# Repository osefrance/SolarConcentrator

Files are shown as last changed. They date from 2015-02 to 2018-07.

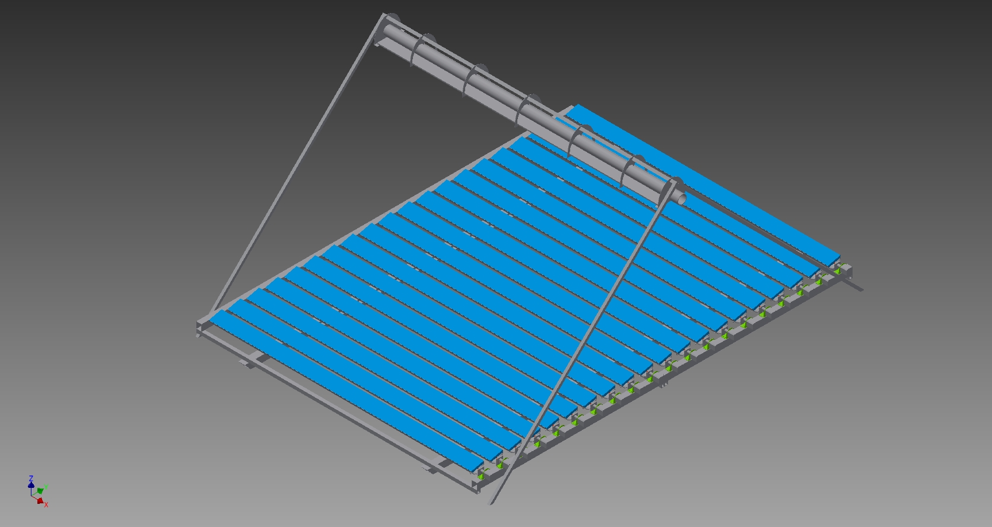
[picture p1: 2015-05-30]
Design3D/Inventor/Assemblage_général_N-S.jpg

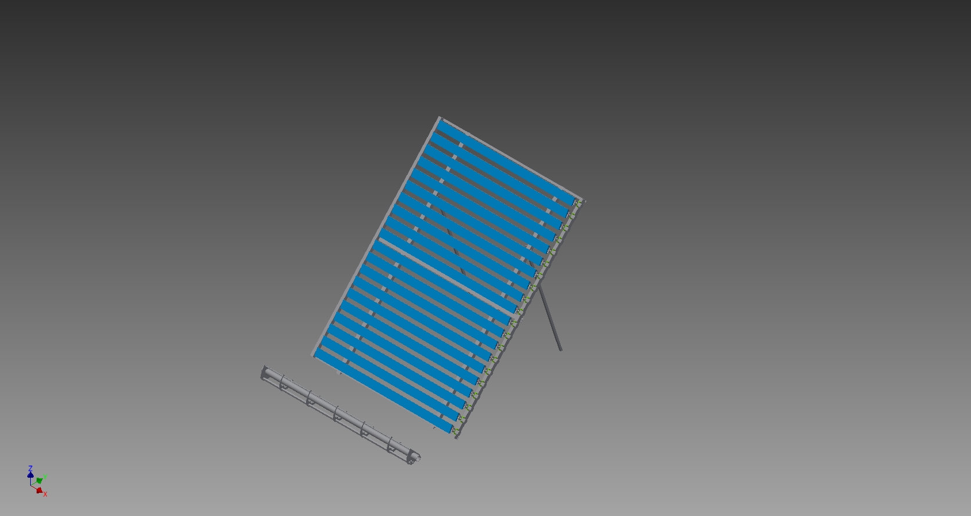
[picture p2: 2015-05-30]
Design3D/Inventor/Assemblage_général_E-O.jpg

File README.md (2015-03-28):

# SolarConcentrator
Open Hardware Solar concentrator - Linear Fresnel Reflector

The OSÉ Solar concentrator programs and designs are licensed under the GPL V2, GPL V3 or 
Attribution-ShareAlike 4.0 International based on the most appropriate license for the type of work.

The full text of the license GPL is available here:  
http://www.gnu.org/licenses/old-licenses/gpl-2.0.html
http://choosealicense.com/licenses/gpl-3.0/
The creative common license is available here http://creativecommons.org/licenses/by-sa/4.0/

See also:
     http://en.wikipedia.org/wiki/GPL 

more information on this open hardware Solar concentrator can be found here: http://wiki.osefrance.org/doku.php?id=wiki:concentrateursolaire

its authors are voulunteers of Open Source Ecologie (French chapter of Open Source Ecology) www.osefrance.fr

#Présentation générale
#Objectif

L'objectif du projet est de fabriquer un concentrateur solaire, c'est à dire, un dispositif permettant de collecter l'énergie thermique solaire, c'est à dire :

    capter et concentrer le flux solaire sur un absorbeur,
    assurer l'extraction de la chaleur pour son utilisation a posteriori.

Les usages et grandeurs de référence sont définies par la suite.
Contexte

Le développement du produit aura lieu au sein de l'association Open Source Écologie en collaboration avec toute personne se sentant un lien pour le projet. Il sera réalisé de manière à s'inscrire dans le contexte de l'économie open source sans contrevenir aux dispositions de la propriété intellectuelle (brevets existants) et aux normes en vigueur (dispositif sous pression).

Le concentrateur solaire a été sélectionné parmi les 50 machines du Global Village Construction Set (GVCS). Il fait partie des dispositifs permettant la production primaire d'énergie.

Le changement climatique et la dépendance actuelle aux énergies fossiles nous montrent la nécessité d'une transition écologique où les énergies renouvelables, et en particulier le solaire thermique, doivent jouer un rôle prépondérant. De plus, le choix du solaire thermique est motivé par le constat que environ 40% de l'énergie consommée par l'industrie en Europe est utilisée pour générer de la chaleur à des températures inférieures à 400°C.
Utilisation : usages et finalité

Nous préparons un développement en plusieurs étapes pour apprendre et progresser au fur et à mesure. Pendant les phases de design 3D et de développement, nous prévoyons de construire une maquette de table pour tester la forme générale et l’automatisation. Ensuite, un démonstrateur sera présenté pendant le forum Alternatiba, le 26 septembre 2015. Enfin, au cours de l’année 2016, un prototype grandeur nature (de 10 à 15 m²) sera conçu sur la base des connaissances engrangées.
#Démonstrateur (phase actuelle)

L'objectif est de présenter la technique de la concentration solaire dans un but de diffusion des savoirs et de sensibilisation. Il est nécessaire d'aboutir à un produit fonctionnel, d'encombrement réduit, fonctionnant en France. La température atteinte sera fonction des optiques concentration et de la surface de miroir mais n'est pas une exigence.
Prototype

Les prototypes seront conçus pour une finalité productive, adaptables sur une large plage de latitudes et dans des lieux isolés. Les usages visés sont variés : cuisson, procédés artisanaux ou industriels utilisant de la chaleur moyenne température (250°C max).
Solution retenue

Il existe différentes technologies de concentration du rayonnement solaire.

Schéma du concentrateur et définition des axes. (1) Miroir de Fresnel ou collecteur; (2) facettes du miroir; (3) récepteur.

La solution que nous avons retenue est un concentrateur solaire plan, à symétrie axiale, avec deux étages de concentration. La concentration primaire est réalisée par un miroir de Fresnel, la concentration secondaire par un concentrateur parabolique composé (CPC) sur l'absorbeur situé au foyer. Cette solution a été retenue pour sa simplicité de fabrication et d'utilisation.

Plus précisément, le miroir de Fresnel ou collecteur (1) concentre le rayonnement sur une ligne sur laquelle se trouve le récepteur (3). L'orientation globale du concentrateur solaire (CS) est fixée par l'axe du récepteur (axe x). Le suivi solaire selon un axe perpendiculaire (axe y) peut être réalisé aisément grâce à la rotation des facettes (3) du miroir de Fresnel. Par contre, la variation d'angle d'incidence parallèle à l'axe du CS (saisonnier ET quotidien) induit une translation entre l'image réfléchie par le collecteur et le récepteur, c'est à dire des pertes supplémentaires aux extrémités du récepteur (end loss).

Figure: schéma du concentrateur et définition des axes. (1) Miroir de Fresnel ou collecteur; (2) facettes du miroir; (3) récepteur.
#Sous-projet : Démonstrateur
#Géométrie

Le miroir est horizontal et l'axe du CS (axe x) est orienté Nord-Sud. Cependant, le démonstrateur a vocation à être utiliser pour l'expérimentation donc une certaine flexibilité dans le positionnement entre le miroir et la structure supportant le récepteur est demandée.
Contraintes particulières
Surface de miroirs (utile) (m2) 	4
Fluide thermique d'échange 	Eau sous pression
“Scalabilité” 1) 	Pas nécessaire
Alimentation électrique 2) 	Indifférent
Dimensions au sol (m) 	6*6 maximum
Hauteur (m) 	h = 2 ± 10%
Poids 	
Coût (€) 	< 1000 3)
Compatibilité design open source 	Au maximum 4)
Implantation 	Paris latitude = 48°N
Livraison 	1/09/2015

De plus, on essayera d'utiliser au maximum des logiciels Open source. Le design étant réalisé en France, les plans utiliseront le système métrique et les normes de dessin françaises.
Schéma de liaison

#Schéma de liaison
http://wiki.osefrance.org/doku.php?id=wiki:concentrateursolaire#schema_de_liaison

#Planning
http://wiki.osefrance.org/doku.php?id=wiki:concentrateursolaire#planning

équipes

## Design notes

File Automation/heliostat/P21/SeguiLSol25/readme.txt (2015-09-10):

//**************************************************************
//  Open Souce Écologie - Solar Heliostat controller
//  Name: SeguiLSol25 - README file
//  Authors: Andrea Sannuto @ndrsan, Jean Walter, ... (other contributors add yourself here)
//  Website: www.osefrance.fr  @OSE_Fr
//  Rev 001 
//  Date 08 April 2015
// This Readme files is meant to collect all the intended modification that need to be integrated into the software.
// this software is released under the GPL V.3 
// for more recents update, check out the git page: https://github.com/osefrance/SolarConcentrator
// http://bit.ly/1JnwSGd
//**************************************************************

it features a simple microstepping of 1/16th of 200 full steps stepper motor and makes a microstep every 54seconds or so.

will need to add:

release 1:
- change routines to State-machine instead of using delay
- reset to 0 position using an optical sensor (as interrupt)
- first setup on the morning (need rtc implementation) using 2 light sensors on the absorber edges (sensors as interrupts)
- last setup on the evening in order to understand the error and use the new delay time for the day after.
release 2:
- multiple mirrors using an IC (need wire implementation)
release 3:
- safety shut off of the mirrors
- statistical information
...

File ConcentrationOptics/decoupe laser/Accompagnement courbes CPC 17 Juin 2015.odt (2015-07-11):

Jean Boubour à Orianne et François

Voici le tracé du CPC selon le fichier du 17 Juin 2015, avec en pièces jointes des fichiers .DXF et .PDF pour causer à la machine laser.

S'il te plait François tu voudrais bien , si possible, envoyer un feu vert à Orianne pour qu'elle trace des profils pour une maquette ?

A +

Jean

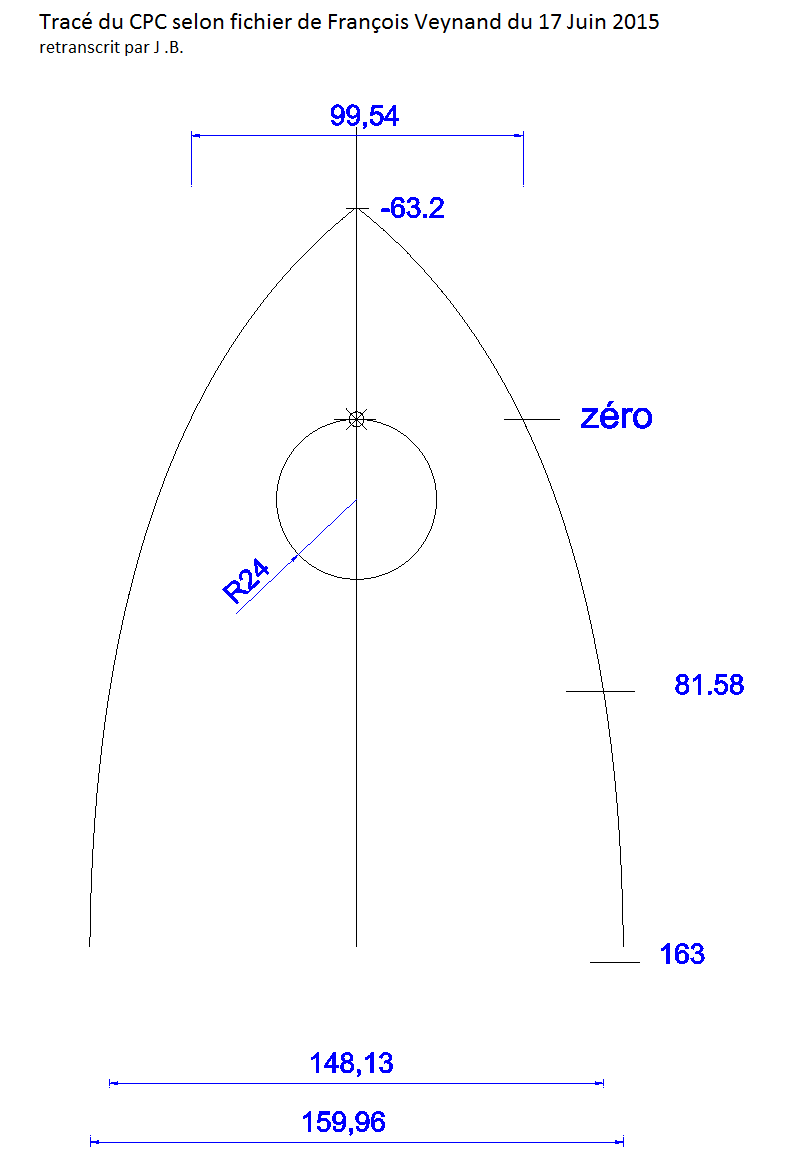
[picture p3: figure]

Dessin des pièces et des entretoises d'assemblage – CPC tracé du 17 Juin 2015

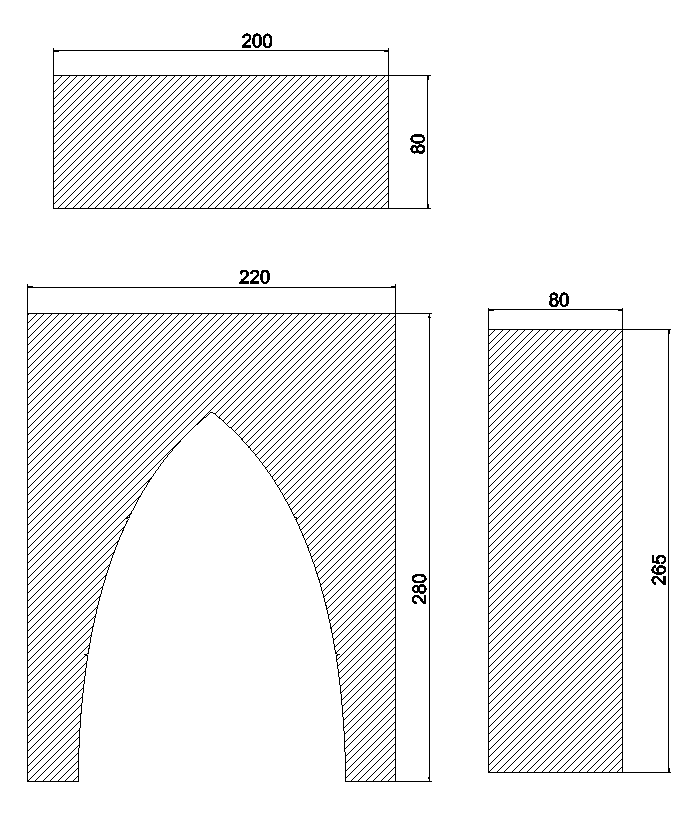
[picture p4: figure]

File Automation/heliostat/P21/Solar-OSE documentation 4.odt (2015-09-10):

Manuel de construction du Concentrateur Solaire Thermique Linéaire de Fresnel
par Open Source Ecologie

Contributeurs :

Andrea, Hugo, Cyril, Oriane, Jean, François, Clément, Tim, Manu, …

Table des matières

# Introduction

## Informations générales

### Coût

1000-1500€ de matériel à affiner

### Temps de réalisation

100-150h ?

### Niveau de difficulté technique

Expert : besoin de savoir-faire notamment pour le circuit hydraulique, surtout dans le cas d’un usage de vapeur sous pression.

## Résumé, accroche

Vous êtes agriculteur et souhaitez transformer vous-même vos produits pour leur donner une plus grande valeur ajoutée ? Vous êtes artisan ou petit industriel et souhaitez réduire vos coûts énergétiques et l’empreinte écologique de vos produits ?

Le concentrateur solaire Open Source Ecologie est fait pour vous : vous pourrez extraire vos huiles essentielles, cuire vos confitures, stériliser vos bocaux, purifier de l’eau, rendre du bois imputrescible, alimenter vos procédés en vapeur jusqu’à 250°C…

Vous pourrez combiner les usages pour utiliser pleinement votre installation. Elle viendra par exemple en appoint pour le chauffage d’eau chaude sanitaire, le séchage de produits, ou encore l’alimentation d’un hammam !

## Conditions d’émergence

Ce concentrateur solaire vise à rendre accessible la chaleur solaire aux petits producteurs, artisans, micro-industries. L’utilisation de l’énergie solaire favorise ainsi une meilleure distribution de l’activité économique sur le territoire. La création de valeur ajoutée de manière décentralisée peut notamment dynamiser les territoires ruraux.

L’utilisation optimale du concentrateur est pour des besoins de chaleur entre 100°C et 200°C. On peut envisager des usages jusqu’à 250°C, ainsi que des usages complémentaires en dessous de 100°C. Ce sont donc plus de la moitié des besoins en chaleur de l’industrie qui sont concernés.

## Historique

L’énergie solaire est depuis toujours la plus grande source d’énergie disponible sur la terre : de manière directe (chauffe-eau solaire, séchoir solaire, cuiseur solaire, centrale solaires thermiques, photovoltaïque), ou indirecte (vent, biomasse, hydraulique, géothermie de surface).

L’utilisation directe de l’énergie solaire existe depuis longtemps. Depuis quelques années, elle se développe plus intensément. De nombreux industriels développent des technologies pour produire de l’électricité ou de la chaleur. Les connaissances se diffusent rapidement dans le monde de la recherche. Mais arrivé au stade commercial, le partage des solutions techniques est plus frileux. L’avancement technologique est donc quelque peu ralentit. En proposant une technologie libre, nous permettons de construire une expérience citoyenne de cette technologie solaire à concentration. Nous encourageons l’utilisation et le travail sur cette technologie, pour l’améliorer et répondre aux besoins de la transition énergétique de manière efficace et accessible.

Les concentrateurs linéaires de Fresnel sont une technologie jeune au niveau industriel, par rapport aux concentrateurs cylindro-paraboliques, sur lesquels des centrales industrielles sont en utilisation aux USA depuis les années 1980. Depuis les années 2000, une centrale Linéaire de Fresnel produit de l’électricité en Espagne. D’autres centrales pilotes sont également en fonctionnement. Un concentrateur solaire Linéaire de Fresnel alimente une laiterie en Sardaigne depuis 2013.

## Principe de fonctionnement

# Conception

## Champ de miroirs

### Structure support

### Facette miroir

facette alternative, moins chère, mais moins recyclable et plus difficile à construire pour une même qualité

## Récepteur

### Structure support

### Cintres

### Réflecteur CPC

### Tube absorbeur / chaudière

### Montage

## Système de suivi

### Moteurs

### Capteurs optiques

### Circuit de contrôle-commande

### Code logiciel

## Exemple d’usage

### Hammam

#### Circuit hydraulique

#### Structure

### Cuiseur

#### Circuit hydraulique

#### Structure

# Réalisation (building time) /documentation time/

## Matériel

### Matériaux

### Outillage

## Champ de miroirs (3j) /5h/

### Structure support (1j)

Etape 1 : Découper les barres

Découper 2 barres de 25x25 mm sur 2130 mm de longueur qui servent de support aux deux barres principales : 2 barres de 30x40 mm sur 1430 mm de longueur. Par exemple utiliser une meuleuse.

Etape 2 : Pointer et percer les trous sur le tube rectangulaire 30x40

Les deux barres de support des facettes de miroirs doivent être percées précisément de deux trous tous les 143 mm. La position de ces trous garantit le parallélisme des facettes entre elles. C’est important pour que toutes les facettes réfléchissent la lumière sur une même ligne. Travailler au millimètre.

Imprimer le gabarit sur du papier bristol en utilisant par exemple une découpeuse laser en mode découpeuse et traceur. Utiliser le plan disponible sur le fichier. Le gabarit est proposé en 2 parties, qu’il suffit d’assembler en joignant précisément les deux morceaux par simple contact. Positionner le gabarit sur le tube carré en veillant bien à ce que le papier soit d’aplomb sur les bords du tube et aux extrémités. Fixer le gabarit avec du ruban adhésif. Attention : si le tube carré est soudé par l’intérieur sur une face, il faut percer sur cette face. En effet, en perçant depuis la face opposée, le foret serait dévié à l’approche de la soudure.

Poinçonner précisément l’emplacement des trous marqués sur le gabarit avec un pointeau et un marteau.

Percer au foret de 6 mm, avec une perceuse à colonne. Utiliser un foret suffisamment long pour percer le tube carré de part en part.

Etape 3 : Pointer et percer les trous aux extrémités des tubes du cadre

Il s’agit de percer à chaque extrémité des 4 tubes, les deux trous de liaison qui assurent (dans une certaine mesure) le maintien de la forme carrée du cadre.

Marquer en rayant les tubes, l’emplacement des trous comme l’indique le schéma : les 2 trous sont placés à 10 mm et 30 mm sur la largeur du tube de 40 mm et centrés à 12.5 mm sur la largeur du tube de 25 mm. De cette manière, les tubes sont fixés d’aplomb, à leur extrémité.

Percer au foret de 6 mm, avec une perceuse à colonne. Utiliser un foret suffisamment long pour percer le tube carré de part en part (au moins 60mm pour percer les 2 tubes à la fois, en cas de rattrapage).

Etape 4 : Assembler les 4 barres

Positionner les tubes carrés sur une table : les tubes de 25x25mm d’abord, puis par-dessus les tubes 30x40mm en appui sur la face de 40mm aux extrémités des tubes de 25x25mm. Les fixer à chaque angle avec une vis M6 de 60mm de long. Ajuster le positionnement des tubes en contrôlant l’angle droit avec une équerre. Si la deuxième vis ne rentre pas dans les deux tubes, ajuster l’alignement des trous en passant un coup de perceuse à main de part en part. Répéter l’opération aux quatre angles pour compléter la fixation.

Etape 5 : Découper les supports des moteurs et des facettes

Découper les pièces support des moteurs et des axes des facettes, en utilisant le fichier , à la découpeuse laser. Il faut 20 pièces supports de moteurs et 40 pièces support d’axe des facettes (un support à chaque extrémité de facette).

Etape 6 : Fixer les supports sur le cadre

Fixer les supports des moteurs sur le tube, côté extérieur. Le moteur et l’axe viennent se fixer au-dessus du tube, donc leurs supports doivent dépasser vers le haut.

### Facette miroir (2j)

Etape 1 : Préparer les tubes carrés

Découper les tubes d’aluminium de 40x20 mm à 2000 mm de longueur (ou les acheter directement à cette dimension). Percer un trou de 5 mm centré dans la largeur, à 100 mm de chaque extrémité. Tarauder ce trou pour des vis de 6 mm de diamètre (M6).

Etape 2 : Préparer les axes

Découper 40 tiges de 8mm de diamètre de 20 cm de longueur chacune. Créer un méplat à 147mm de l’extrémité de la tige qui sera placée à l’extérieur du tube aluminium.

Etape 3 : Préparer les supports des axes

Dans une planche de bois de 100mm d’épaisseur, découper à l’imprimante laser 40 cales intérieures (coins arrondis) et 40 cales extérieures (coins droits) selon le fichier.

Etape 4 : Préparer les miroirs

Découper des bandes de tôle miroir de 2000 mm de longueur et 100 mm de largeur. On peut utiliser un cutter. Si la plaque de base n’est pas assez longue, on peut découper deux portions de 1000 mm de longueur pour couvrir chaque facette. Veiller à ne pas déformer le miroir, pour conserver une planéité parfaite des facettes : 0,1° de déformation génère 1 cm de décalage sur le récepteur.

Etape 5 : Assembler les axes

Pour chacune des 40 tiges axes : insérer une cale intérieure à l’extrémité intérieure de la tige (proche du méplat). Insérer une cale extérieure à l’autre extrémité et laisser dépasser 47 mm de tige. Poser l’axe et ses cales sur un support plan, avec l’axe en bas, de sorte à s’assurer que les cales sont parallèles entre elles. Dans cette même position, orienter le méplat vers le haut (photo). Fixer les cales avec un point de colle (araldite).

Etape 6 : Assembler les facettes

Insérer les axes et leurs cales dans les tubes en aluminium. La tige axe doit être tangente à la face opposée au trou fileté. Ainsi, le méplat fait face à la vis. Fixer la vis dans le trou fileté jusqu’à appuyer l’axe au niveau du méplat. L’axe est alors maintenu en position dans la longueur et latéralement.

Coller les bandes de miroirs sur les tubes en aluminium. Veiller à ce qu’ils soient bien centrés dans la largeur.

### Améliorations possibles

Impression du gabarit papier : sur une imprimante classique A4, quelle procédure ?

Ajouter un tube en diagonale pour éviter les mouvements de type parallélogramme déformable.

La solution pour la facette avec tube carré en aluminium de 40x20mm, sur lequel est posé le miroir, est une amélioration. La première solution envisagée a été abandonnée : Solution avec demi-tube de PVC. (1-2h par 2 facettes ? => 10h. A optimiser) Découper 10 tubes PVC en deux dans la longueur (un gabarit peut aider à couper correctement le tube), formant ainsi 20 supports de miroirs. Découper 6 demi-disques en bois par facette, avec un trou pour positionner l’axe du moteur. L’axe est maintenu par 2 demi-disques à chaque extrémité. 2 demi-disques supplémentaires permettent de renforcer la structure et supportent les miroirs. Les bandes de 10cm de large de miroir sont collées sur la surface du demi-tube de PVC et s’appuie aussi sur les 6 demi-disques de bois. Le problème principal est la mauvaise résistance de la facette en torsion : l’ensemble de la lumière réfléchie ne serait pas collecté sur la même ligne, ce qui est rédhibitoire pour de bonnes performances optiques…

## Récepteur (2j) /10h/

### Structure support (1j)

Etape 1 : Préparer les barres du "tipi"

Découper 4 barres 30x30 sur 2300 mm ( ?) de longueur : une coupe droite + une coupe à 45°. Percer selon le plan les trous pour l’assemblage des pieds du "tipi" (1 trou/barre), la fixation du récepteur (1 trou par barre), la fixation des barres inférieures dans la longueur (2 trous par barre), la fixation de la barre transversale (1 trou par barre). Vérifier la longueur totale de la barre : la longueur qui importe pour le positionnement des trous est celle mesurée depuis la base du pied.

Découper 4 plats de 30mm de large et 5mm d’épaisseur et 40mm (check) de long. Percer et tarauder les plats à 1 cm du bord pour fixer un pied réglable à vis de 8mm de diamètre. Souder les plats aux extrémités coupées à 45°. On obtient ainsi un pied horizontal réglable.

Etape 2 : Préparer les barres inférieures, les renforts, la barre transversale et le câble transversal.

Découper les barres inférieures : 4 barres 20x20 sur 2200 mm (check) de longueur (Amélioration : ou une barre carrée de 20x30 ou 20x40 ?). Souder 2 barres côte à côte pour former une barre rectangulaire. Les percer aux extrémités selon le plan.

Découper les barres de renfort : 2 barres 20x20 sur 1000 mm de longueur avec un angle de 45° aux deux extrémités. Découper 2 plats de 20x3 sur 100 mm de longueur et 2 cornières 30x50 (profilé en L) sur 100 mm de longueur. Percer les 2 plats et les 2 cornières selon le plan. Souder les cornières et les plats selon le plan aux extrémités de la barre de 100 mm. Les barres de renfort sont prêtes. Bien veiller à obtenir un angle de 45° entre la surface extérieure du plat et la barre, ainsi qu’entre la surface extérieure de la cornière et la barre. Cela garanti l’angle droit entre la barre du "tipi" et la barre inférieure.

Découper la barre transversale : un plat de 30x5 sur 2150 mm de longueur. Les percer aux extrémités selon le plan : les trous sont distants de 2120 mm (à 1500mm du trou d’assemblage du "tipi").

Découper le câble de 2mm de diamètre sur une longueur de 2000 mm environ. Ajuster sa longueur de manière à obtenir une longueur totale de 2120 mm entre les trous de fixation sur les barres du "tipi" : former une boucle à une extrémité et pincer à l’étau l’anneau de serrage sur le câble ; mesurer l’élément d’ajustage de la longueur en position ouverte (Lmax) et couper le câble à une longueur de (2120 - Lmax + 40 mm) de manière à former la boucle pour une longueur de câble finale (2120 - Lmax).

Etape 3 : Assemblage et montage de la structure à revoir…

Assembler à l’horizontale, les barres 2 à 2 pour former les deux supports en "tipi", à l’aide d’une vis de diamètre 10 mm. Visser les pieds réglables sur leur support, au bas des barres des "tipis".

Fixer les barres inférieures au pied des barres du tipi : cela fixe la distance entre les "tipis". Positionner les barres de renfort de 100 mm avec des serre-joints ou des pinces étaux selon le schéma. Vérifier que : (1) la barre du "tipi" et la barre inférieure forment un angle de 90°, (2) le plat et la cornière sont bien parallèles, respectivement à la barre inférieure et à la barre du "tipi". Percer la barre du tipi et la barre inférieure dans le prolongement du trou de l’élément de renfort (plat et cornière). Si le foret n’est pas assez long, percer d’abord le trou côté élément de renfort. Puis, marquer le point opposé au premier trou et percer le deuxième trou depuis l’autre côté de la barre.

A 2 personnes, lever la structure pour former les tipis. Une troisième personne positionne la barre transversale au nord, côté où il y a les renforts, en la fixant avec 2 vis. Ensuite, elle fixe le câble côté sud et ajuste sa longueur à 2120. La structure doit alors tenir en équilibre, mais c’est mieux si une personne continue de maintenir le "tipi" côté sud. Pendant ce temps, les deux autres personnes peuvent apporter le récepteur et le positionner sur le tipi. Il reste à passer les vis pour fixer le tube du récepteur aux barres du "tipi". Cette opération termine de rigidifier la structure.

### Structure du récepteur (1h)

Poutre centrale

Découper une barre de 30x30mm de 2300mm de longueur.

Profilés latéraux en L

Découper deux profilés en L 30x60mm de 3mm d’épaisseur et 2100 mm (à vérifier) de longueur.

Percer les trous de fixation aux cintres.

Percer les trous de fixation à la jonction (cf ci-dessous).

Souder un plat à chaque extrémité du L (pour fixation sur le "tipi"…) (à valider, en coordination avec la longueur)

Jonction de la poutre centrale et des profilés latéraux en L

Découper, percer, souder selon le plan.

Cintre

Imprimer les 10 cintres à la découpeuse laser, dans une planche (lamellé collé par exemple) de 10mm d’épaisseur.

Imprimer 2 cintres pleins, sans l’évidage pour le réflecteur secondaire, pour fermer le récepteur aux extrémités.

### Réflecteur CPC (3h)

#### Objectif

Mettre en forme le réflecteur secondaire Concentrateur Parabolique Composé (CPC)

#### Matériaux et Outillage

- Le squelette du CPC
- Tôle alu finition miroir de 0.5mm
- Cutter
- réglet de 1m et équerre métallique
- 3 grands serre-joints
- Perceuse et forêt de 4mm
- X vis M4 et rondelles

#### Pliage des miroirs secondaires

Etape 1 : Découpe d’une tôle miroir / Cutting the mirror sheet (15 min)

Au cutter, découper un rectangle de 340 par 680 mm de la tôle miroir. Veillez à protéger la surface du miroir pendant l’opération et effectuer la découpe au dos. Il faut passer plusieurs fois au cutter pour entamer le métal puis il cède en le pliant successivement dans un sens puis dans l’autre.

With a cutter, cut a 340 by 680 mm rectangle of mirror sheet. Mind to protect the reflective surface of the mirror during the operation and to work on the back side. One needs to run the cutter several times to bite the metal and to fold back and forth in order to detach it.

Etape 2 : Tracé des traits de pliage / Marking folding lines (30 min)

Au cutter, tracer les traits de pliage selon le plan suivant. Il faut passer une fois au cutter pour marquer proprement le pliage mais ne pas fragiliser la structure du métal.

With the cutter trace the folding lines following the plan below. Run the cutter in order to mark the line without going through and fragilizing the metal.

Etape 3 : Perçage / drilling (30 min)

Percer les trous de fixation du miroir selon le plan suivant. Les trous oblongs peuvent êtres percés en penchant la perceuse de chaque côté jusqu’à obtenir un trou de 7 mm de long (voir suggestions d’amélioration en fin de section Récepteur à ce sujet).

Drill the holes

Etape 4.1 : Pliage / folding (1h)

Nous proposons ici une méthode simple en termes d’outillage. Une plieuse peut faire l’affaire si elle plie nettement le miroir. Il est plus facile de travailler à deux personnes pour bien plier le miroir.

On commence par un pli sur une ligne centrale. Choisir une table rigide, qui ne fléchit pas, avec un bord à angle droit net. Placer la tôle miroir face réfléchissante en bas, de manière à visualiser facilement les traits de pliage gravés sur la tôle. Plier selon le premier pli apparent (le deuxième pli central est caché sous la planche de maintien). Protéger le miroir avec une épaisseur de feuille de papier. Maintenir fermement la tôle miroir avec une planche fixée de chaque côté par un serre-joint. Choisir une planche bien rigide, avec un bord à angle droit net, de longueur supérieure à la tôle. Avec une autre planche au bord à angle droit net, de la longueur de la tôle, appuyer par-dessous pour imposer un pli de 20 à 30° à la tôle (environ la moitié de 45°). Bien s’assurer que la planche est contre le bord de la table. Couvrir la planche de papier, pour protéger la face réfléchissante du miroir. Bien appuyer de manière homogène sur toute la longueur de la tôle, pour avoir un pli régulier.

Poursuivre avec la même méthode pour le deuxième pli central : il suffit de relâcher le maintien de la tôle et de la sortir de quelques millimètres pour faire apparaître la marque du deuxième pli. Refixer. Appuyer près du pli est d’autant plus important à cette étape. Le premier pli peut se renforcer, mais il faut imposer un angle au deuxième pli de 20 à 30°. L’angle total est alors de 45° environ.

Appliquer deux fois la même méthode pour chacun des plis latéraux (un de part et d’autre): fixer la tôle fermement par la bande latérale de 20 mm. Cela permet d’avoir une meilleure prise sur la tôle à plier. Imposer un angle à 90° net. Bien appuyer contre la ligne de pliage.

Etape 4.2 : Courbure / folding (1h)

La tôle de 0.5 mm est assez rigide. Un préformage est nécessaire à maintenir le réflecteur dans la position imposée par les cintres. Nous proposons ici une méthode simple en termes d’outillage, qui donne un résultat correct mais nettement perfectible (toute suggestion d’amélioration est bienvenue). Il est plus facile de travailler à deux personnes pour bien courber le miroir sur toute sa longueur.

Installer une planche rigide de 15 cm de large maximum, surélevée de 10cm par rapport à la table. Cela permet de mettre en forme une partie du réflecteur, sans être gêné par l’autre volute.

Une première courbure est imposée par un tube de 10cm de diamètre : utiliser un tube d’évacuation en PVC par exemple. Placer la tôle face réfléchissante vers le haut. Aligner le premier pli central au bord de la planche de manière à laisser la deuxième volute libre vers l’avant. Protéger le réflecteur avec du papier. Fixer le tube au bord de la planche, le plus proche possible du centre du CPC. Veiller à ce que le tube soit parallèle à la tôle. Bien serrer avec les serre-joints (compatibles avec 25 cm de hauteur). Avec une planche peu large ou une barre métallique, relever la volute pincée sous le tube. Bien plaquer la tôle contre le tube sur toute sa longueur pour imposer une courbure régulière tout le long de la courbe. Insister sur la fin pour avoir une courbure jusqu’à la partie latérale du CPC.

Répéter l’opération sur l’autre volute.

Une deuxième courbure autour d’un tube de 4 cm est ensuite imposée à la partie centrale. Placer le tube de 4 cm de dans la même position que le tube de 10 cm. Attention à positionner le tube le plus proche possible du bord de la planche. La déformation du miroir sera ainsi donnée le plus proche possible du centre. Pour améliorer la courbure proche du centre, il est aussi possible de positionner le miroir dans l’autre sens. Le pincer en laissant environ 7 cm de miroir dépasser en mesurant depuis la pliure centrale. Ainsi, en relevant le miroir, on plaque la tôle sur le tube jusqu’au centre. En pratique, le résultat est un peu difficile à obtenir car on n’a pas de bras de lebier. En effet, il faut faire attention à ne pas déformer la pliure, ce qui risquerait de la casser.

Répéter l’opération sur l’autre volute.

Félicitations : le réflecteur secondaire CPC est prêt à être monté.

### Tube absorbeur / chaudière ()

Etape 1 : Souder la chaudière

Couper un tube en laiton de 55mm de diamètre extérieur d’une longueur de 1900mm.

Souder aux extrémités des raccords, selon le plan (conseils complémentaires : cf Simon).

Etape 2 : Rendre la chaudière absorbante

Gratter le tube au papier de verre fin ou bien à la paille de fer. Dégraisser le tube (préciser ?).

Oxyder le tube en appliquant un liquide oxydant au pinceau. Laisser sécher plusieurs heures. Rincer abondamment à l’eau pour enlever les cristaux de l’oxydant. Répéter l’opération 2 ou 3 fois (à valider).

### Montage (3h)

Etape 1 : Placer les cintres sur le tube carré

Couper le tube carré à 2.2m de longueur.

Placer les 10 cintres sur le tube carré, avec un espacement approximatif de 22 cm de distance.

Etape 2 : Préparer le plat métallique de fixation latérale du réflecteur secondaire

Couper le plat à 2 m de longueur. Percer le plat selon le plan, diamètre 4 mm : 10 trous, 1cm du bord aux extrémités et distance équidistante entre, soit 22 cm. Fraiser l’entrée du trou avec une mèche de 8 mm. L’important est que la vis à tête plate affleure à la surface du plat (sans dépasser). C’est la position de ces trous qui donnent la rigidité au récepteur en imposant la distance exacte entre les cintres. Attention à bien percer les deux plats de manière identique, pour que les cintres soient bien perpendiculaires à l’axe du récepteur.

Etape 3 : Fixer le réflecteur secondaire

Placer les 3 portions de réflecteurs préformés dans leur emplacement, avec un chevauchement type tuiles de toiture « dessus-dessous ». Commencer par fixer entièrement un côté : placer le plat latéral sur un côté du réflecteur préformé. Placer les vis dans chaque trou, afin de fixer la barre. Pincer l’écrou pour visser sans abimer le cintre.

Etape 4 : Placer le tube dans la cavité (ajuster sa position en hauteur et latéralement)

Etape 6 : Placer les capots réfléchissants aux extrémités de la cavité du récepteur

Etape 5 : Positionner les L et la vitre (avec un joint en dessous et au-dessus), les fixer au récepteur par les cintres et la jonction.

Etape 6 : Etanchéifier la cavité du récepteur avec du mastic (spécial feu)

Etape 7 : Remplir le récepteur d’isolant tout autour de la cavité

Etape 8 : Fermer avec le capot

Etape 8 : Positionner le récepteur sur sa structure.

### Points à améliorer

Pour percer les trous oblongs sans abimer le foret, percer deux trous en poinçonnant le centre des trous à une distance de 3 mm (le deuxième trou est souvent moins réussi, un petit limage peut améliorer le résultat) ou 4 mm (un petit limage est nécessaire pour enlever la matière entre les deux trous.

Position des trous : peut-être percer les trous après avoir percé le plat ? Normalement, les trous oblongs donnent déjà une marge de ce point de vue.

Le pliage du réflecteur secondaire est perfectible. La tôle miroir est difficile à mettre en forme, notamment dans sa partie centrale. Avec la méthode proposée, le miroir ne suit pas bien la forme du cintre dans sa partie centrale. Une idée est de travailler les deux volutes séparément pour donner plus facilement la courbure forte au centre. Le pli central serait alors formé après la courbure.

Dans la méthode proposée, la courbure centrale étant difficile à obtenir, le pli central nécessaire est donc moins important. Nous proposons donc de donner un angle réduit par rapport à la forme théorique, d’où l’angle de 45°. En donnant l’angle théorique de 90°, le réflecteur risque de casser au montage à cause du dépliage subit pour s’ajuster au cintre.

Le pliage à la plieuse à gouttière n’est pas satisfaisant d’après notre test : le pli n’est pas anguleux. Il a tendance à tordre le miroir dans un sens non désiré.

Pour la courbure serrée, un tube de 5 cm (au lieu de 4 cm) pourrait également être testé : cela permettrait d’utiliser le tube récepteur.

Position du tube carré : le placer à plat, au lieu de sur la pointe, permettrait de réduire la hauteur du CPC avec la même rigidité des cintres.

## Système de suivi (2j) /10h/

### Moteurs

Fixer les moteurs aux supports de la structure.

### Capteurs optiques, boîtier de contrôle et câblage

### Circuit de contrôle-commande

Schéma logique à insérer.

### Code logiciel

Lien vers le code.

## Exemple d’usage (3j) /10h/

### Hammam

#### Circuit hydraulique

#### Structure

### Cuiseur

#### Circuit hydraulique

#### Structure

=>Fabrication time estimate : 10j (+5j de marge ;) x 10h/j = 150h

=> Documentation time estimate : 35h, avec la marge : 50h.

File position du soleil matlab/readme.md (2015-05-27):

- [jour.m](https://github.com/ooriane/solarcal_matlab/blob/master/position%20du%20soleil/jour.m) calcul du numero du jour en fonction de la date (jour/mois)  
- [heure_legale.m](https://github.com/ooriane/solarcal_matlab/blob/master/position%20du%20soleil/heure_legale.m) calcul de l'heure légale (= réelle, telle que lue sur une montre) en fonction de l'heure solaire, du jour considéré et de la longitude  
- [delta.m](https://github.com/ooriane/solarcal_matlab/blob/master/position%20du%20soleil/delta.m) calcul de la déclinaison en fonction du jour de l'année
- [soleil_ah.m](https://github.com/ooriane/solarcal_matlab/blob/master/position%20du%20soleil/soleil_ah.m) et [soleil_xyz.m](https://github.com/ooriane/solarcal_matlab/blob/master/position%20du%20soleil/soleil_xyz.m) calcul des coordonnées du Soleil soit en (azimut, hauteur) soit en coordonnées cartésiennes en fonction du jour, de l'heure solaire et de la latitude  
- [soleil_simple.m](https://github.com/ooriane/solarcal_matlab/blob/master/position%20du%20soleil/soleil_simple.m) trace la course du Soleil pour un jour et une latitude donnés  

Pour plus d'informations sur les variables et les calculs, voir la page de référence du wiki [Trajectoire du Soleil](http://wiki.osefrance.org/doku.php?id=wiki:trajectoire_du_soleil)

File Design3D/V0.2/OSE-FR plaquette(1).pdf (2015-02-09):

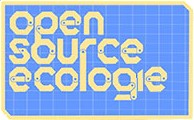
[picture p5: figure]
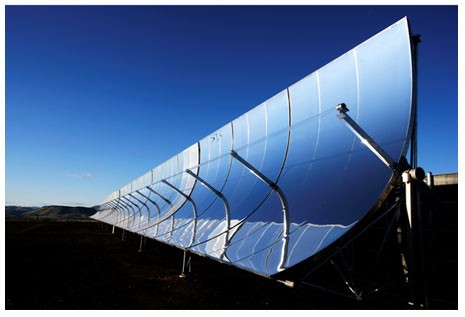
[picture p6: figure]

Open Source Ecology France - www.osefrance.fr - osefrance@gmail.com - @OSE_Fr

# Open Source Ecology France

## L’association

Open Source Ecology France est une association créée en Septembre 2014. Elle se donne pour objet d’œuvrer pour le développement et l’appropriation citoyenne de l’Outil Libre dans le contexte de la transition écologique.

Ses actions visent à offrir aux citoyens la documentation mais aussi les savoirs et les compétences nécessaires à l’appropriation de certains outils productifs et des énergies qui les meuvent. Elle souhaite ainsi contribuer à l’émergence d’un nouvel ordre économique fondé sur un accès facilité et généralisé aux outils productifs.

L’association s'inscrit dans les pas du mouvement Open Source Ecology (OSE) né aux États-Unis en 2003. Elle contribue aux 50 projets de OSE (le GVCS) (http://www.osefrance.fr/?page_id=44) et les adapte aux spécificités françaises et européennes. Plus largement, l’association participe à l'émergence du mouvement open source en France, mène des activités éducatives, etc.

L’association fonctionne par des contributions publiques et privées volontaires. Ses productions sont ouvertes et libres. Une gouvernance innovante, proche de la sociocratie, est envisagée pour parvenir à une auto-organisation circulaire.

Pour les activités économiques susceptibles de découler de ses travaux, l’association souhaite encourager la création d’un écosystème de coopératives extérieures fournissant les services autour des produits développés.
(Liens : notre vision , (http://www.osefrance.fr/?page_id=15) nos statuts) (http://cloud.osefrance.org/public.php?service=files&t=377ccab4786017a8f6fec7f5433231cd)

## Premier projet en développement : Concentrateur Solaire

Un concentrateur solaire est un
dispositif qui concentre la lumière du
soleil pour en exploiter l’énergie thermique.

La lumière qui arrive sur une large zone (quelques dizaines de mètres
carrés | dans | notre | projet) | est
concentrée par un jeu de miroirs sur un petit absorbeur. Dans l’absorbeur circule un fluide (de l’eau par exemple) qui recueille l’énergie
solaire sous forme thermique.

Les différences avec le photovoltaïque sont les suivantes. Le solaire photovoltaïque fourni une énergie polyvalente et précieuse (l’électricité) avec un rendement faible. Le solaire

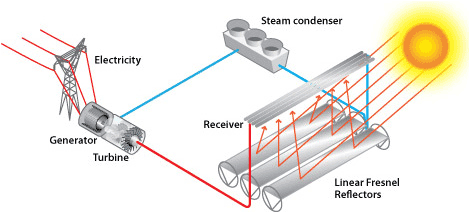
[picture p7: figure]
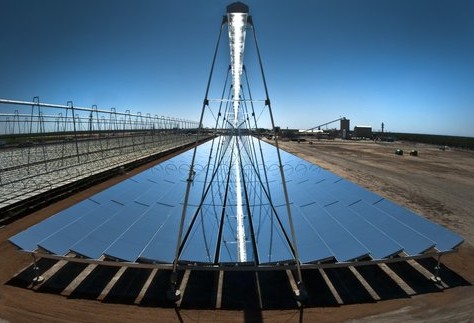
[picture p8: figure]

Open Source Ecology France - www.osefrance.fr - osefrance@gmail.com - @OSE_Fr thermique, quant à lui, fournit une énergie spécialisée (la chaleur) avec un très bon rendement.

Certaines applications concrètes reposent simplement sur l’utilisation immédiate de la chaleur (fours, procédés chimiques, séchage de matériaux, stérilisation, etc).
La cogénération est aussi possible. Il s’agit est de produire à la fois de la chaleur et de l’énergie mécanique ou de l’électricité. Il est alors nécessaire d’ajouter un moteur et un générateur électrique au concentrateur solaire.

Concentrateur Linéaire de Fresnel
Le type de concentrateur que nous cherchons à développer est un concentrateur linéaire de Fresnel. La lumière est focalisée par des miroirs plans sur un tube d’absorption où circule le fluide thermique. Des températures de 200°C à 400°C peuvent être atteintes.

La géométrie de ce type de concentrateur permet d’anticiper des coûts de production et d’entretien plus faibles que les précédents modèles où les miroirs étaient paraboliques.

Les caractéristiques prioritaires du modèle que nous concevons sont la modularité, la durabilité, la fabrication DIY-friendly, ainsi qu’un coût minimal. Les modules auront environ 10 m² de miroirs. Le nombre de modules ainsi que les conditions d’utilisations (températures, pression, type d’énergie et de stockage…) pourront être adapté aux besoins. Le segment économique visé est celui des usages micro-industriels ou artisanaux.

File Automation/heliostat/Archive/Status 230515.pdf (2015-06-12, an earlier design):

# Concentrateur Solaire à lame de Fresnel

# Projet ose.fr Equipe Orientation des miroirs Traqueur astronomique et Optique

Réunion du 25/05/15 La Paillasse

# Participants : Andrea, Chérif, Jean, Philippe, Rémi

23/05/15 | JLWAL | 2

# Objectifs et méthode

## - Principe :

## – L'arduino sait ou il doit aller grâce à son horloge, mais peut détecter un dérive (et corriger) grâce à ses capteurs optiques

## - Il est prévu pour le premier prototype :

### – Un moteur pas à pas par lame miroir

- Une lame miroir directrice pour centrage optique

### – Une modèle math de position solaire

- Azimut uniquement
- Alternative : informer via internet coordonnées solaires

### – Des capteurs optiques sur les bords du récepteur

- Permettant au processeur de centrer les miroirs
- Permettant de corriger les dérives

# Bâti d'essai pour capteurs optiques

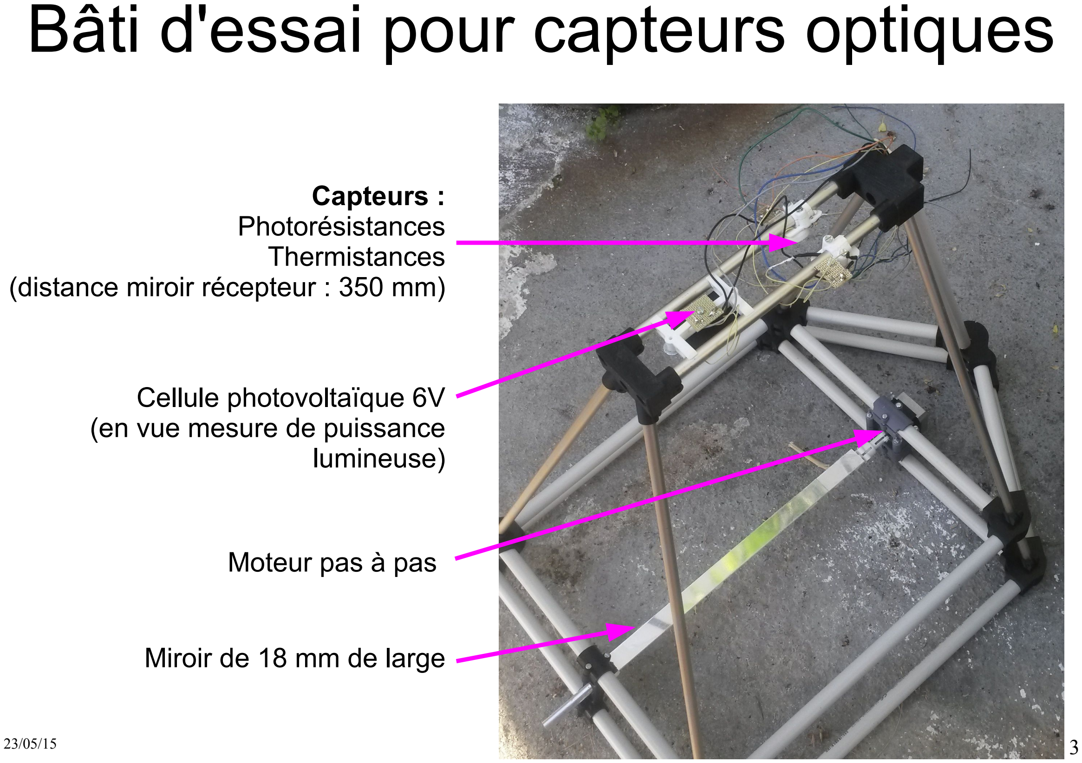
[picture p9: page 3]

Miroir de 18 mm de large

Moteur pas à pas

Cellule photovoltaïque 6V
(en vue mesure de puissance lumineuse)

Capteurs :
Photorésistances
Thermistances
(distance miroir récepteur : 350 mm)

# Capteurs Optiques

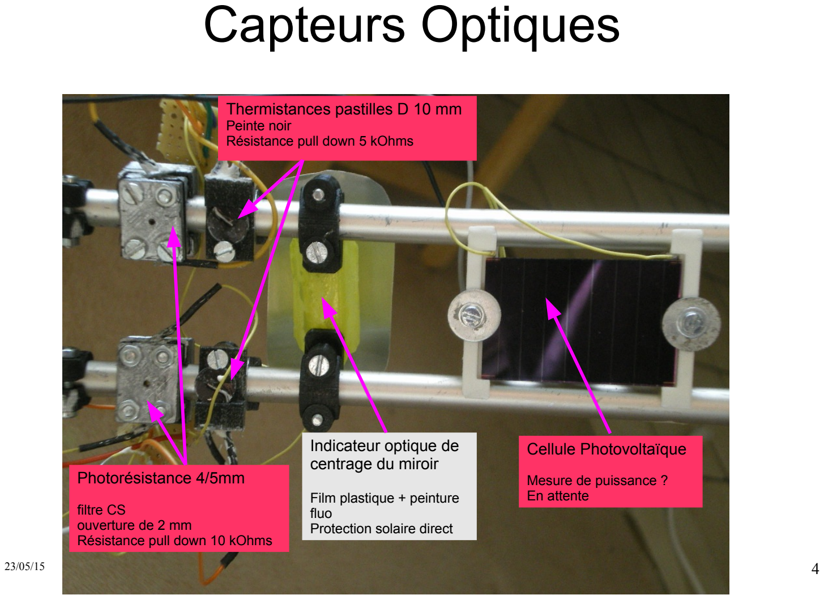
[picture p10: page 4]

Photorésistance 4/5mm

filtre CS
ouverture de 2 mm
Résistance pull down 10 kOhms

Thermistances pastilles D 10 mm Peinte noir
Résistance pull down 5 kOhms

Indicateur optique de
centrage du miroir

Film plastique + peinture
fluo
Protection solaire direct

Cellule Photovoltaïque

Mesure de puissance ?
En attente

# Branchements

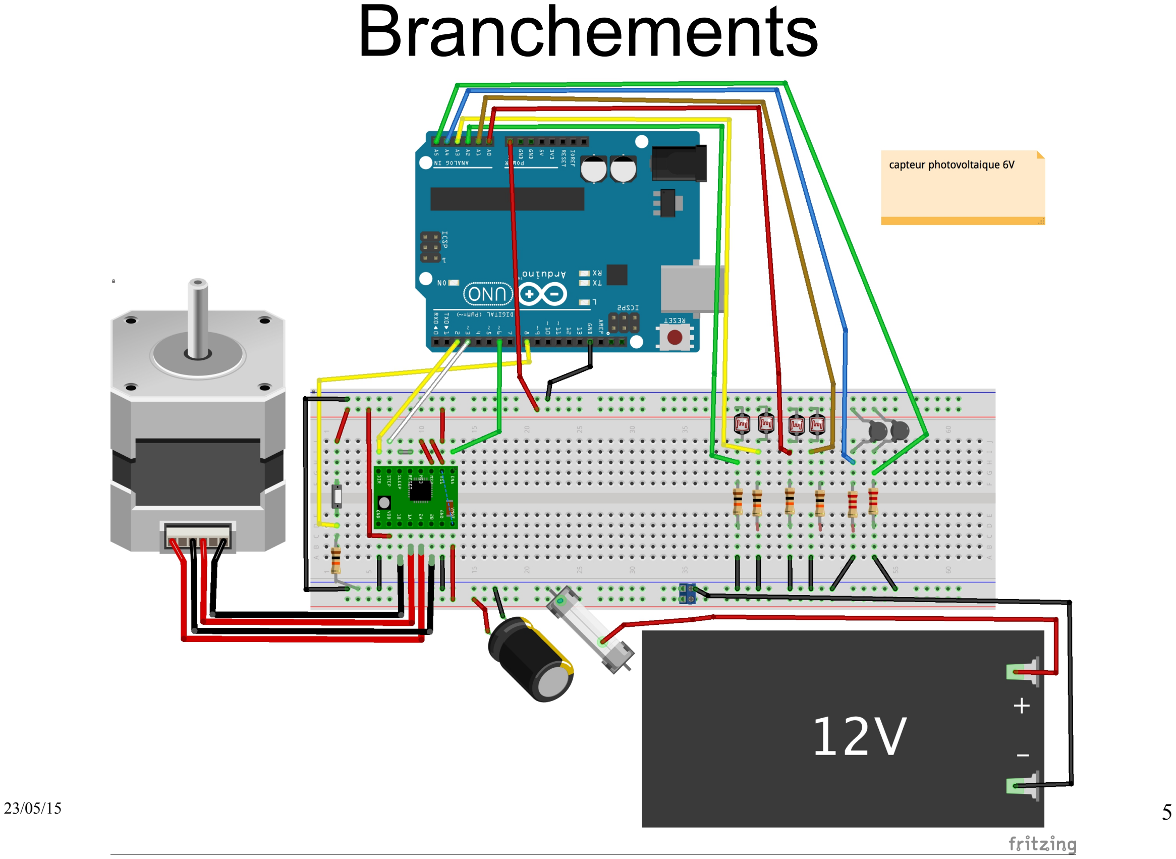
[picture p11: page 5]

# Centrage par photorésistances

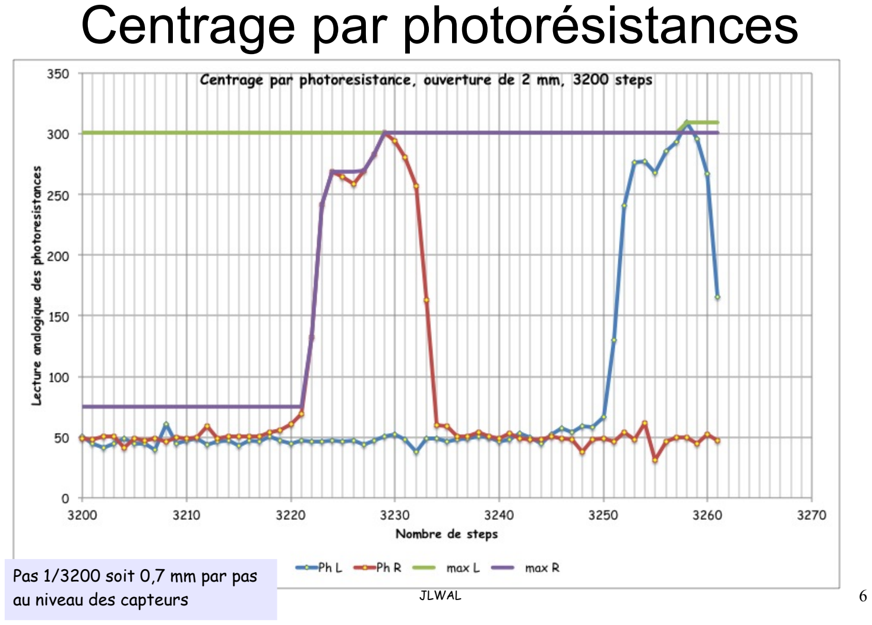
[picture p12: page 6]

Pas 1/3200 soit 0,7 mm par pas au niveau des capteurs

# Centrage par thermistances

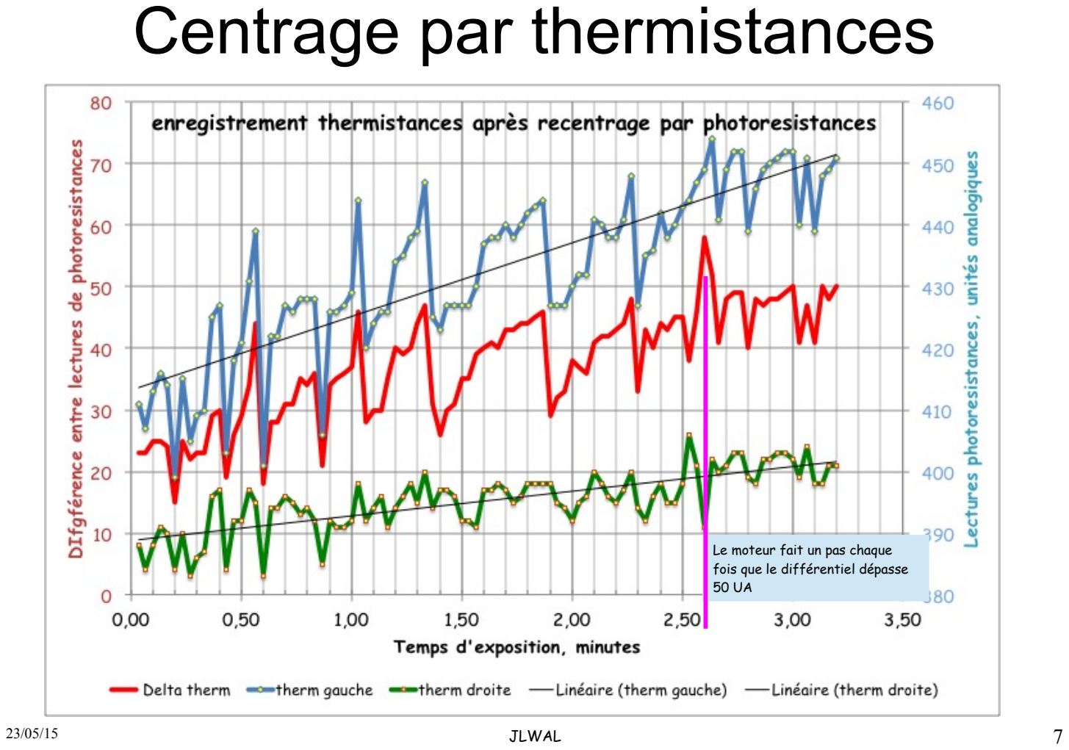
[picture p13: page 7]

Le moteur fait un pas chaque fois que le différentiel dépasse 50 UA

# Avancement et prochaine étapes

# - Bien avancé :

## - Système optiques de centrage

- Thermistances + photorésistances et prgm OK
- Calcul de puissance solaire par cel photovoltaïque en attente

# - A faire avancer :

## - Horloge et calcul azimut solaire versus temps

- pour Arduino Mega

## - Correspondance position miroirs versus azimut solaire - Pilotage des moteurs

- « boite de vitesse » pour scanner à +sieurs niveaux de résolution
- solidité/protection des drivers

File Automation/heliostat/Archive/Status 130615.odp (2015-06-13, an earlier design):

## Concentrateur Solaire à lame de Fresnel

Projet ose.fr

Equipe Orientation des miroirs

Traqueur astronomique et Optique

Réunion du 13/06/15 – La Paillasse, Paris

Participants :

Andrea, Chérif, Fabien, Jean, Oriane, Philippe, Rémi

## Avancement

- Principe :
    - L'arduino sait ou il doit aller grâce à son horloge, mais peut détecter un dérive grâce à ses capteurs optiques et corriger sa trajectoire
- En cours:
  - Horloge et calcul azimut solaire versus temps
    - Alternative aux calculs lourds ; base de données 54 points/jours (15 min) x 24 (deux jours par mois) sur carte SD = une option réalisable ?
    - Horloge en cours d’installation sur une Uno
  - Correspondance position miroirs versus azimut solaire
    - Calculs donnés par Oriane
  - Pilotage des moteurs
    - « boite 2 vitesses » déplacement ou scanner pour centrage
- Bien avancé :
  - Système optiques de centrage
    - Thermistances + photorésistances et prgm OK
    - Calcul de puissance solaire par cellule photovoltaïque : disponible sur bati d'essai

## Azimut vs temps

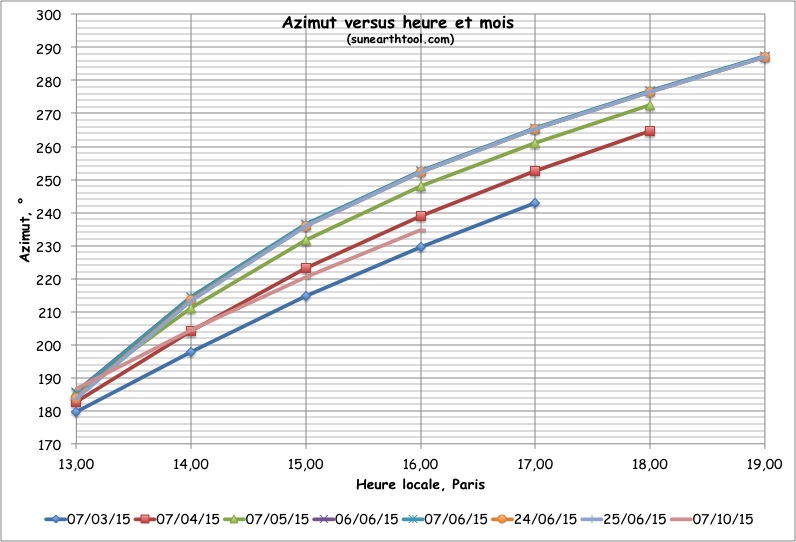
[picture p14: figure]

## Vitesse angulaire azimut solaire

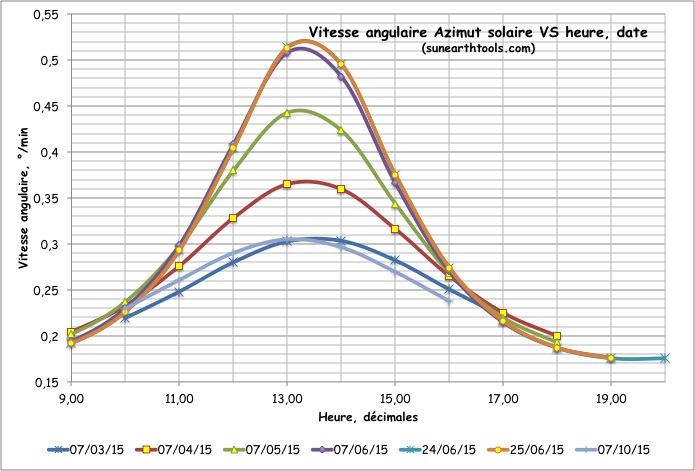
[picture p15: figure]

## Références et sites projet

- Calculs et programmes Arduino
  - Logiciel traqueur horloge
    - http://www.cerebralmeltdown.com/arduino-sun-tracking-heliostat-program-download-page/
  - Calculs position soleil
    - http://herve.silve.pagesperso-orange.fr/solaire
  - Github : dossiers position soleil matlab Oriane
    - https://github.com/osefrance/SolarConcentrator
    - (+ http://forum.osefrance.org/index.php)
- Référence position soleil en ligne
  - Pour calcul de précision en comparaison avec des sites spécialisés
    - http://www.sunearthtools.com/dp/tools/pos_sun.php?lang=fr
    - http://zebulon1er.free.fr/Rayonnement%20solaire%20calculs.htm

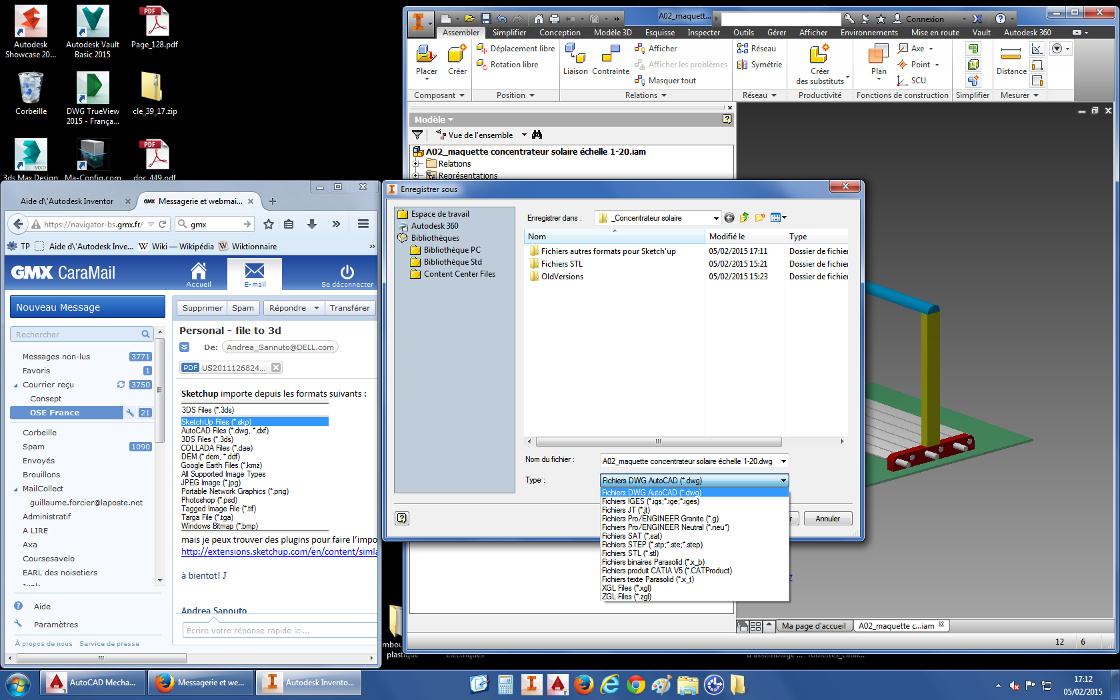
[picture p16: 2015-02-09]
Design3D/V0.2/2015 02 05 Inventor - formats exportables.png

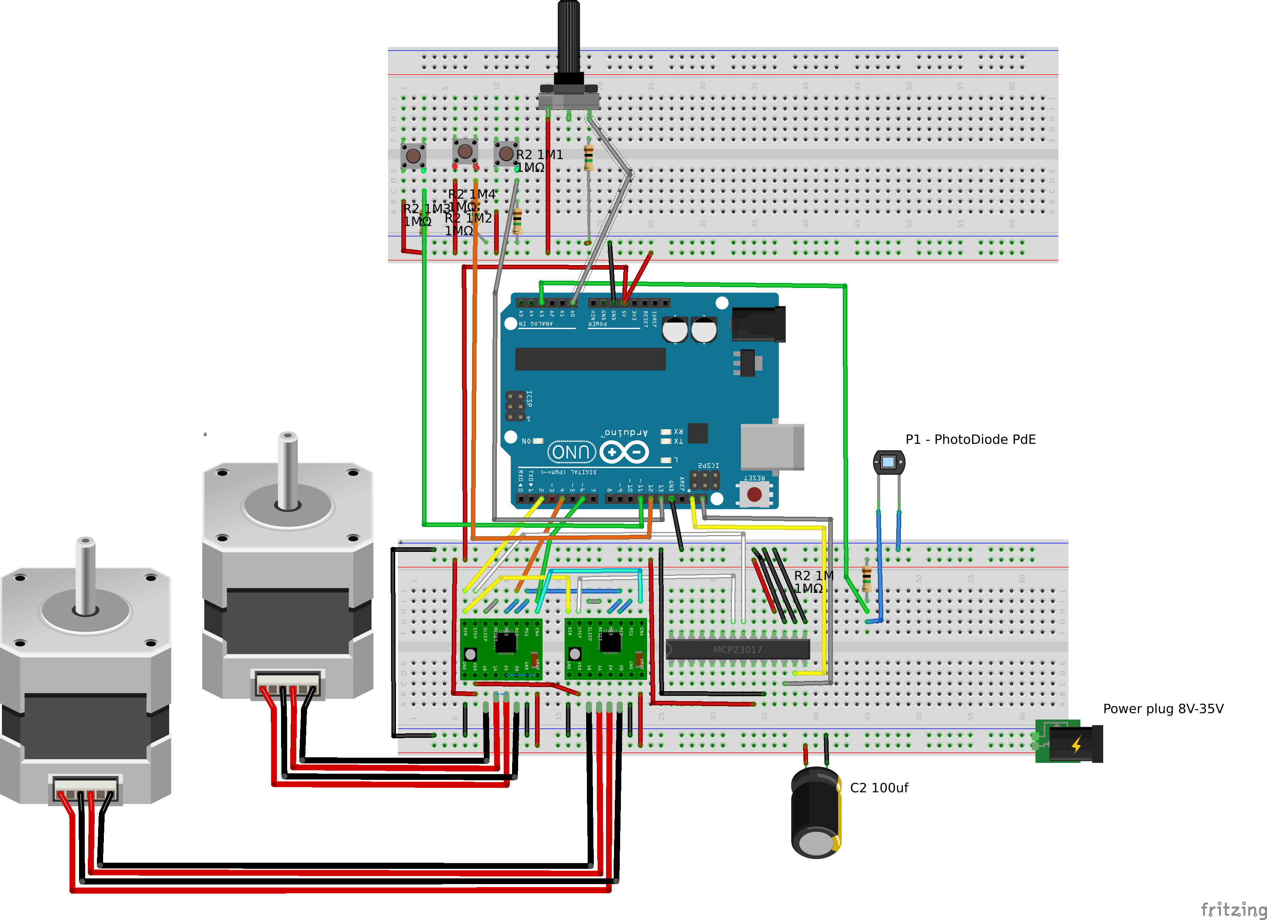
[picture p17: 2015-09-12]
Automation/heliostat/P21/OSE_Heliostat/OSE_heliostat_Control0.21/OSE_Heliostat_Control.021_bb.png

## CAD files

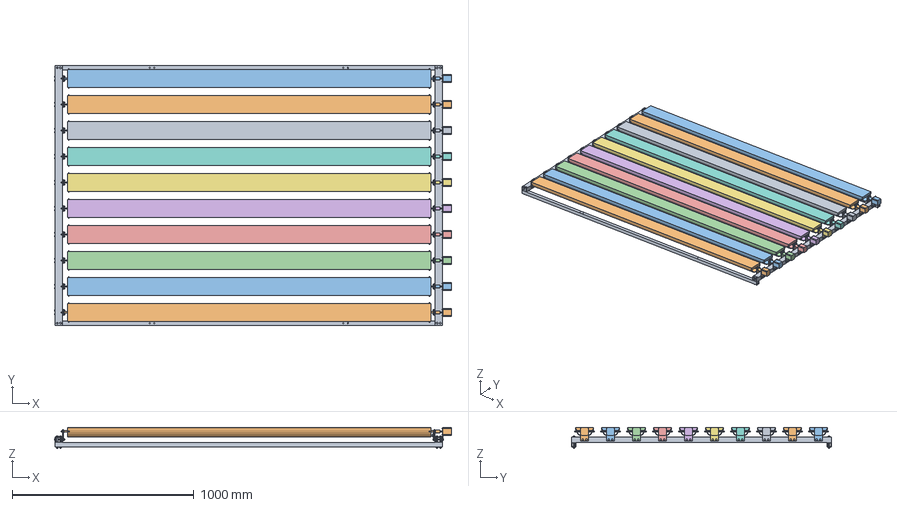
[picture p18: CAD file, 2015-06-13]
Design3D/FreeCAD/ASM CS V2/Concentrateur solaire/Assemblage_cadre-miroir/_Assemblage_cadre-miroir.FCStd
2184.0 x 1430.0 x 118.0 mm
_Assemblage_cadre_01
_Assemblage_miroir_01
_Assemblage_miroir_02
_Assemblage_miroir_03
_Assemblage_miroir_04
_Assemblage_miroir_05
_Assemblage_miroir_06
_Assemblage_miroir_07
_Assemblage_miroir_08
_Assemblage_miroir_09
_Assemblage_miroir_10

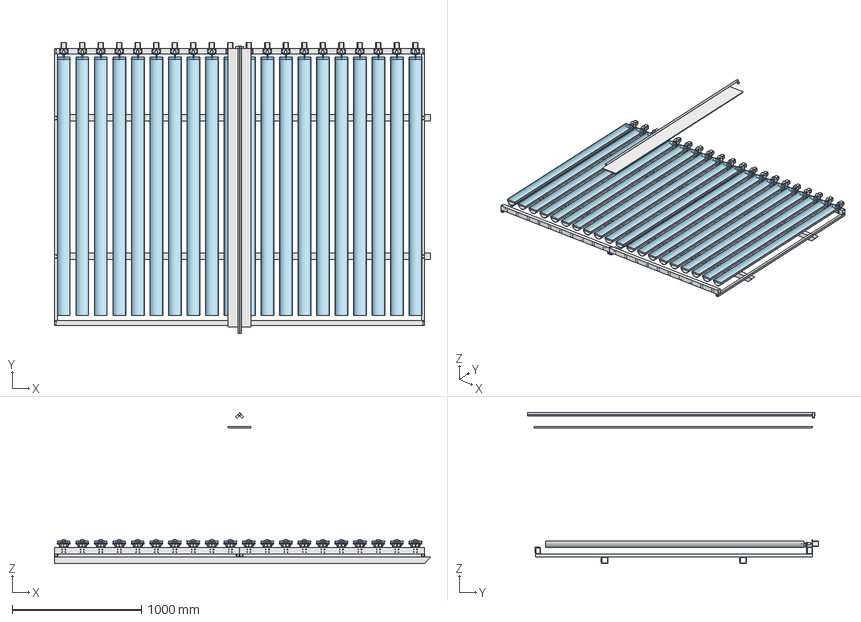
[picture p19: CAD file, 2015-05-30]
Design3D/FreeCAD/Assemblage.FCStd
2905.0 x 2248.0 x 1167.1 mm
Poutre_centrale_20x20x2_L2200
Raccord
Vitre
Accouplement_001
Moteur_001
Demi_tube_sous_miroir_001
Coussinet_autolub_C2-151-8-128_001
Plaque_support_001
Plaque_moteur_001
Capteur_optique_001
Axe_D8_001
Axe_D4_001
Plaque_alveolaire_001
Accouplement_002
Moteur_002
Demi_tube_sous_miroir_002
Coussinet_autolub_C2-151-8-128_002
Plaque_support_002
Plaque_moteur_002
Capteur_optique_002
Axe_D8_002
Axe_D4_002
Plaque_alveolaire_002
Accouplement_003
Moteur_003
Demi_tube_sous_miroir_003
Coussinet_autolub_C2-151-8-128_003
Plaque_support_003
Plaque_moteur_003
Capteur_optique_003
Axe_D8_003
Axe_D4_003
Plaque_alveolaire_003
Accouplement_004
Moteur_004
Demi_tube_sous_miroir_004
Coussinet_autolub_C2-151-8-128_004
Plaque_support_004
Plaque_moteur_004
Capteur_optique_004
Axe_D8_004
Axe_D4_004
Plaque_alveolaire_004
Accouplement_005
Moteur_005
Demi_tube_sous_miroir_005
Coussinet_autolub_C2-151-8-128_005
Plaque_support_005
Plaque_moteur_005
Capteur_optique_005
Axe_D8_005
Axe_D4_005
Plaque_alveolaire_005
Accouplement_006
Moteur_006
Demi_tube_sous_miroir_006
Coussinet_autolub_C2-151-8-128_006
Plaque_support_006
Plaque_moteur_006
Capteur_optique_006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

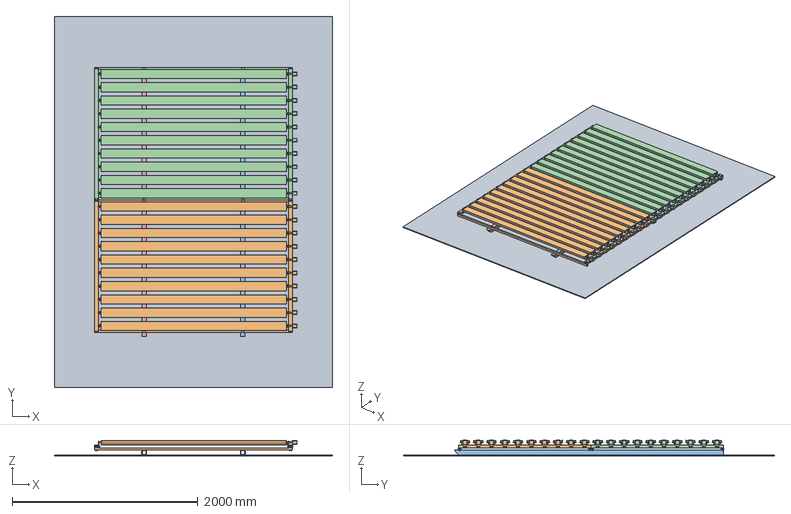
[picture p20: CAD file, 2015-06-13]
Design3D/FreeCAD/ASM CS V2/Concentrateur solaire/_Assemblage_general.FCStd
3000.0 x 4000.0 x 168.0 mm
Sol_01
_Assemblage_cadre_miroir_01
Tube_50x50x3_L2905_01
_Assemblage_cadre_miroir_01001
Tube_50x50x3_L2905_02

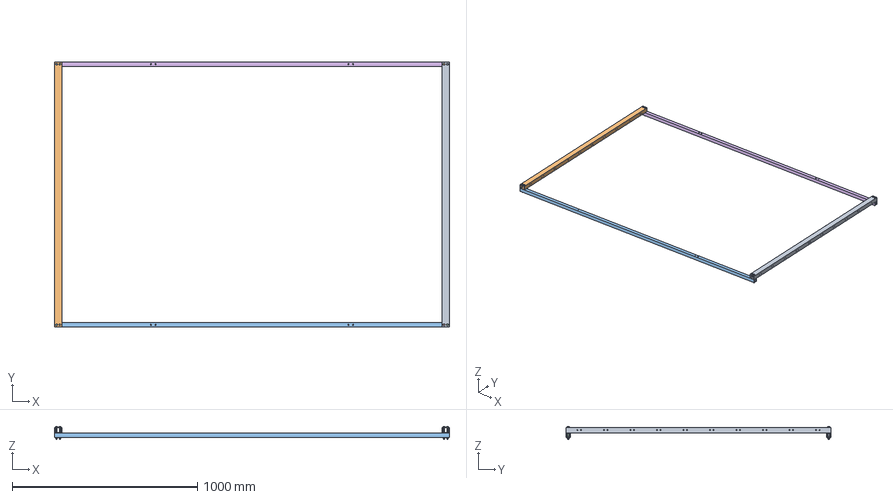
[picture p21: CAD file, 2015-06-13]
Design3D/FreeCAD/ASM CS V2/Concentrateur solaire/Assemblage_cadre-miroir/Cadre/_Assemblage_cadre.FCStd
2130.0 x 1430.0 x 69.0 mm
Tube_40x30x2_L1430_01
Tube_40x30x2_L1430_02
Tube_25x25x3_L2130_01
Hexagon_head_bolt_DINENISO4014_M6_65_01
Hexagon_head_bolt_DINENISO4014_M6_65_008
Tube_25x25x3_L2130_02
Hexagon_head_bolt_DINENISO4014_M6_65_003
Hexagon_head_bolt_DINENISO4014_M6_65_03
Hexagon_head_bolt_DINENISO4014_M6_65_04
Hexagon_head_bolt_DINENISO4014_M6_65_05
Hexagon_head_bolt_DINENISO4014_M6_65_06
Hexagon_head_bolt_DINENISO4014_M6_65_07
Hexagon_nut_ISO4032_M6_01
Hexagon_nut_ISO4032_M6_02
Hexagon_nut_ISO4032_M6_03
Hexagon_nut_ISO4032_M6_04
Hexagon_nut_ISO4032_M6_05
Hexagon_nut_ISO4032_M6_06
Hexagon_nut_ISO4032_M6_07
Hexagon_nut_ISO4032_M6_08

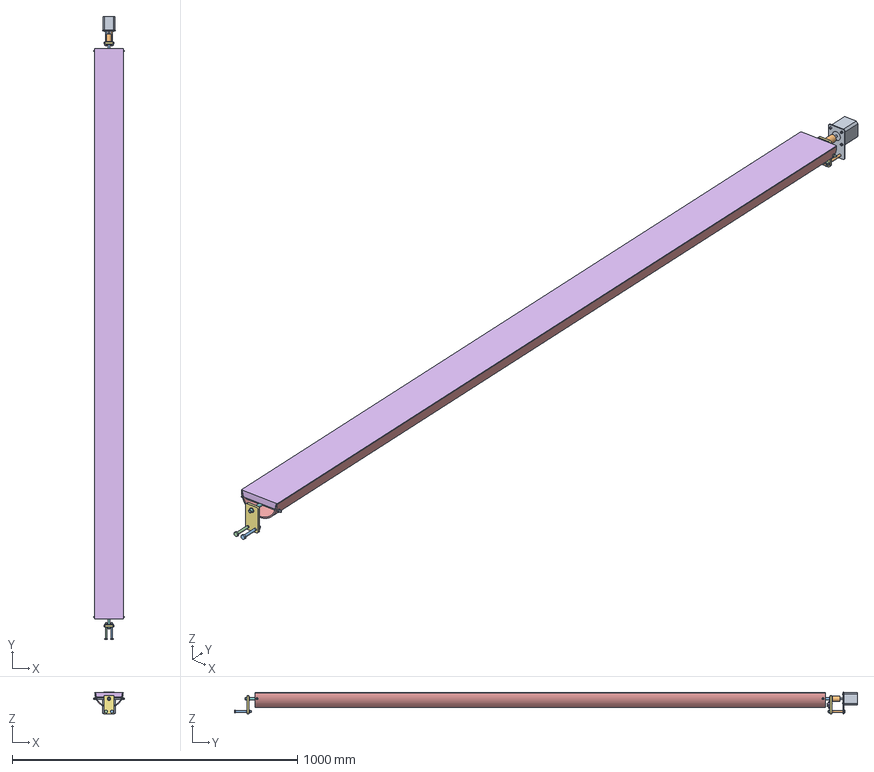
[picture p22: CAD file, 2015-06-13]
Design3D/FreeCAD/ASM CS V2/Concentrateur solaire/Assemblage_cadre-miroir/Assemblage_miroir/_Assemblage_miroir.FCStd
110.0 x 2184.0 x 76.0 mm
Moteur_
Accouplement_
Axe_D8_
Axe_D4_
Demi_tube_sous_miroir_
Plaque_alveolaire_
Plaque_support_
Coussinet_lub_
Plaque_moteur_
Hexagon_head_bolt_DINENISO4014_M6_55_01
Hexagon_head_bolt_DINENISO4014_M6_55_02
Hexagon_nut_ISO4032_M6_01
Hexagon_nut_ISO4032_M6_02
Capteur_optique_01
Plaque_support_G_01
Axe_D8_01
Axe_D4_01
Coussinet_lub_01
Hexagon_head_bolt_DINENISO4014_M6_55_03
Hexagon_head_bolt_DINENISO4014_M6_55_04
Hexagon_nut_ISO4032_M6_03
Hexagon_nut_ISO4032_M6_04
ISO4762_Hex_Socket_Head_Cap_Screw_M3x8_01
ISO4762_Hex_Socket_Head_Cap_Screw_M3x8_02
Hexagon_nut_ISO4032_M4_01
Hexagon_nut_ISO4032_M4_02
Hexagon_nut_ISO4032_M4_03
Hexagon_nut_ISO4032_M4_04
ISO4762_Hex_Socket_Head_Cap_Screw_M3x6_01
ISO4762_Hex_Socket_Head_Cap_Screw_M3x6_02
ISO4762_Hex_Socket_Head_Cap_Screw_M3x6_03
ISO4762_Hex_Socket_Head_Cap_Screw_M3x6_04

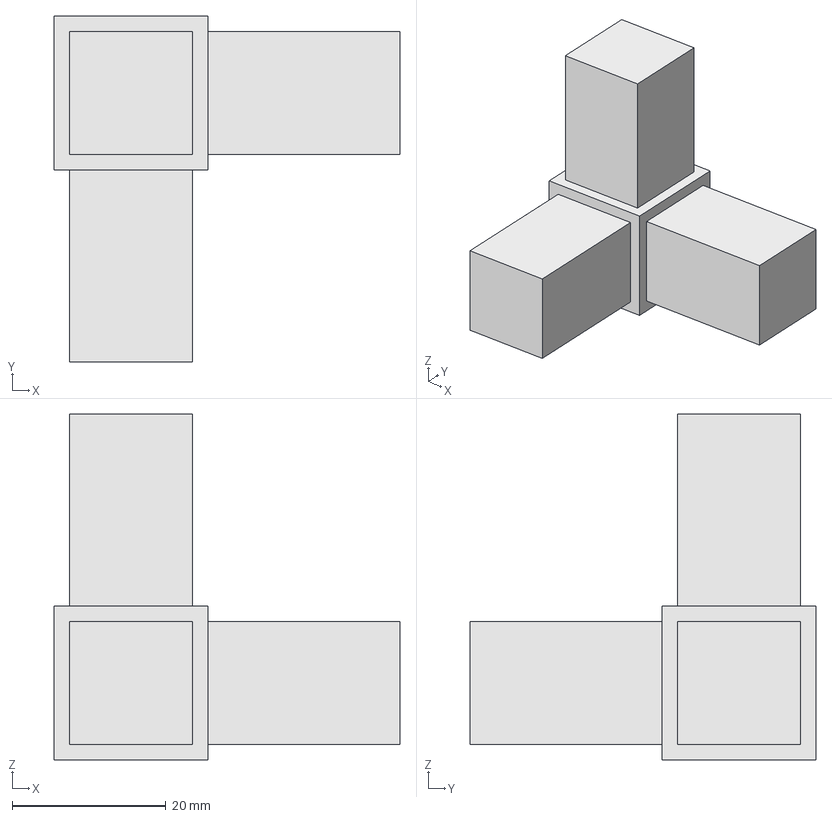
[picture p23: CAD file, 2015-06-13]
Design3D/FreeCAD/ASM CS V2/Concentrateur solaire/Absorbeur/Raccord.FCStd
45.0 x 45.0 x 45.0 mm

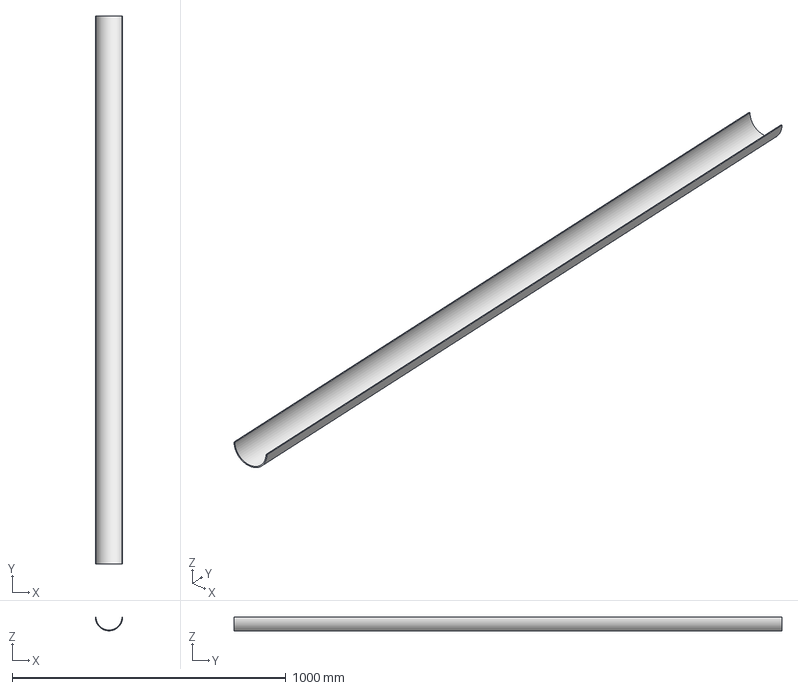
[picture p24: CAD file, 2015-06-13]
Design3D/FreeCAD/ASM CS V2/Concentrateur solaire/Assemblage_cadre-miroir/Assemblage_miroir/Demi_tube_sous_miroir.FCStd
100.0 x 2000.0 x 50.0 mm

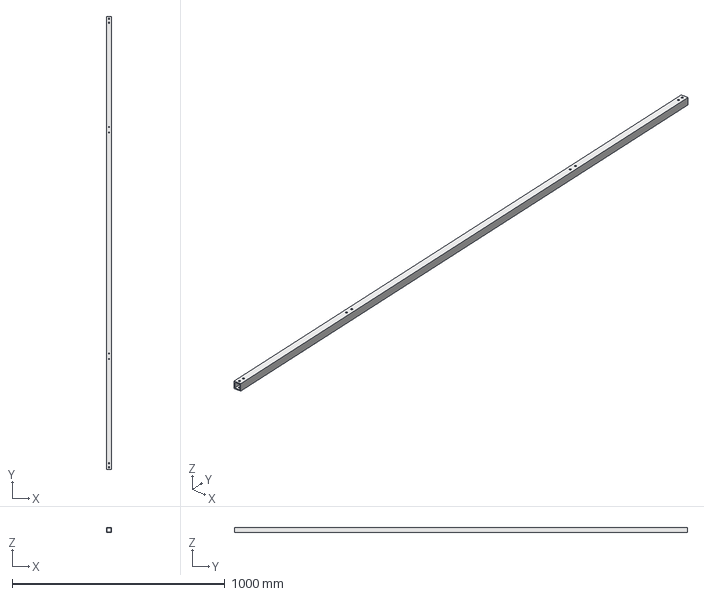
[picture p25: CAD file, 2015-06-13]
Design3D/FreeCAD/ASM CS V2/Concentrateur solaire/Assemblage_cadre-miroir/Cadre/Tube_25x25x3_L2130.FCStd
25.0 x 2130.0 x 25.0 mm

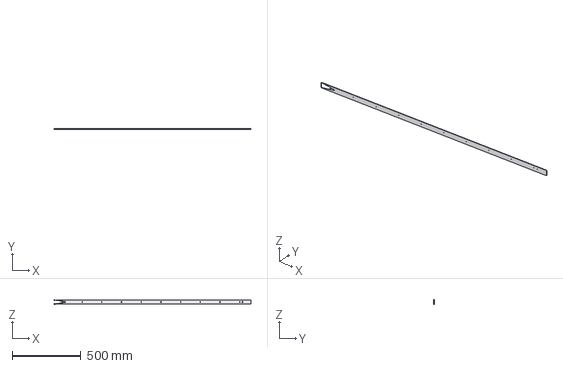
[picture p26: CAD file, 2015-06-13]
Design3D/FreeCAD/ASM CS V2/Concentrateur solaire/Gabarit/gabarit super critique.FCStd
1431.2 x 3.00 x 30.0 mm

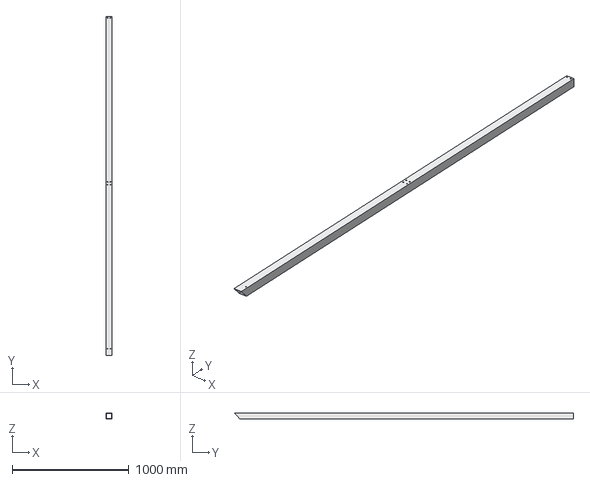
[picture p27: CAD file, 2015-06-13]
Design3D/FreeCAD/ASM CS V2/Concentrateur solaire/Tube_50x50x3_L2905.FCStd
50.0 x 2905.0 x 50.0 mm

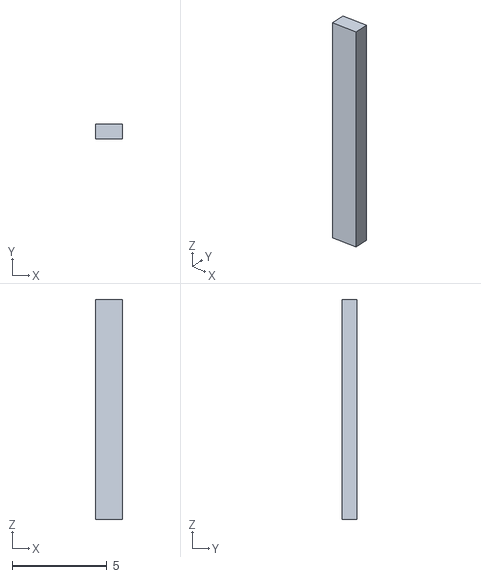
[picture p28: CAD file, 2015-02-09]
Design3D/V0.2/09_pied collecteur.stl
1.40 x 0.8 x 11.6

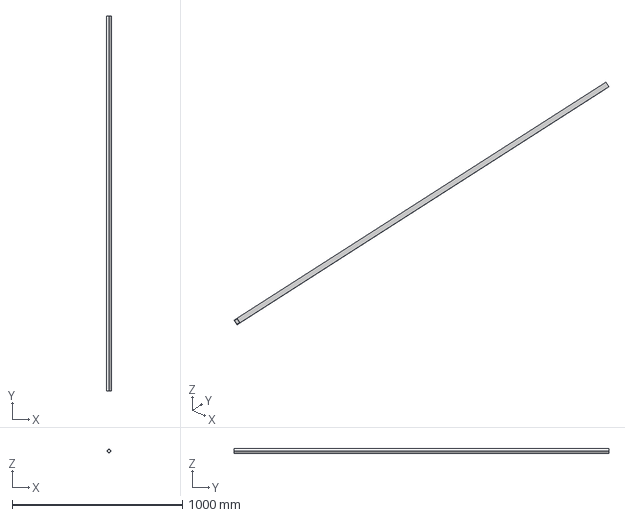
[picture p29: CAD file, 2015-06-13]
Design3D/FreeCAD/ASM CS V2/Concentrateur solaire/Absorbeur/Poutre_centrale_20x20x2_L2200.FCStd
28.3 x 2200.0 x 28.3 mm

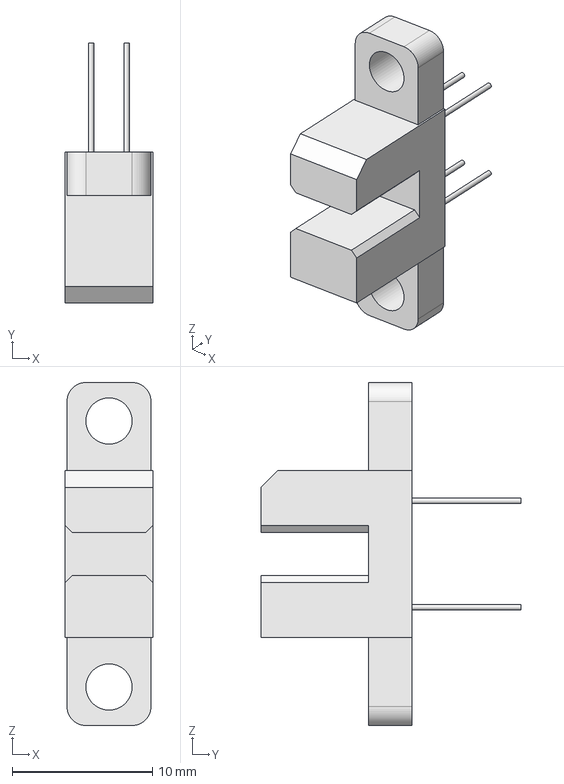
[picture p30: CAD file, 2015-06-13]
Design3D/FreeCAD/ASM CS V2/Concentrateur solaire/Assemblage_cadre-miroir/Assemblage_miroir/Capteur_optique.FCStd
6.30 x 18.6 x 24.5 mm

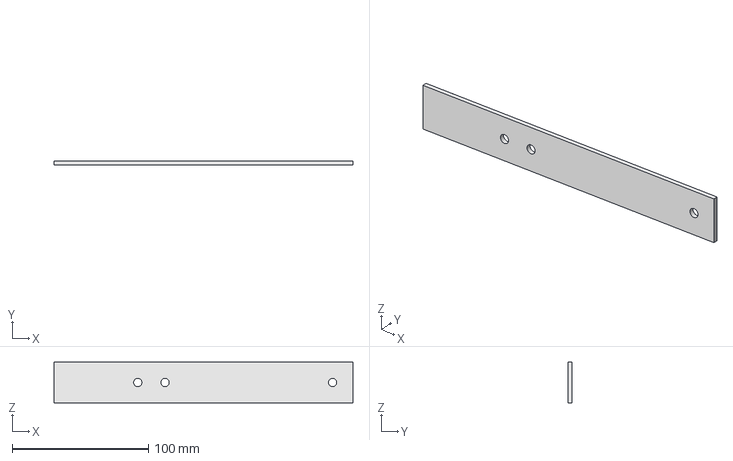
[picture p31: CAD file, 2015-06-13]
Design3D/FreeCAD/ASM CS V2/Concentrateur solaire/Gabarit/gabarit théorique.FCStd
219.5 x 3.00 x 30.0 mm

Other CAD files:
Design3D/V0.2/A02_maquette concentrateur solaire échelle 1-20.stl
Design3D/FreeCAD/ASM CS V2/Concentrateur solaire/Absorbeur/Patron.FCStd
Design3D/FreeCAD/ASM CS V2/Concentrateur solaire/Assemblage_cadre-miroir/Assemblage_miroir/Accouplement.FCStd
Design3D/FreeCAD/ASM CS V2/Concentrateur solaire/Assemblage_cadre-miroir/Cadre/Tube_40x30x2_L1430.FCStd
Design3D/FreeCAD/ASM CS V1/ASM CS.FCStd
Design3D/FreeCAD/ASM CS V1/Accouplement.FCStd
Design3D/FreeCAD/ASM CS V1/Coussinet lub.FCStd
Design3D/FreeCAD/ASM CS V1/Demi tube sous miroir.FCStd
Design3D/FreeCAD/ASM CS V1/Moteur.FCStd
Design3D/FreeCAD/ASM CS V1/Plaque support.FCStd
Design3D/FreeCAD/ASM CS V1/axe 1.FCStd
Design3D/FreeCAD/ASM CS V1/axe 2.FCStd
Design3D/FreeCAD/ASM CS V1/support moteur.FCStd
Design3D/FreeCAD/ASM CS V1/support profilé cadre.FCStd
Design3D/FreeCAD/ASM CS V2/Concentrateur solaire/Absorbeur/Vitre.FCStd
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

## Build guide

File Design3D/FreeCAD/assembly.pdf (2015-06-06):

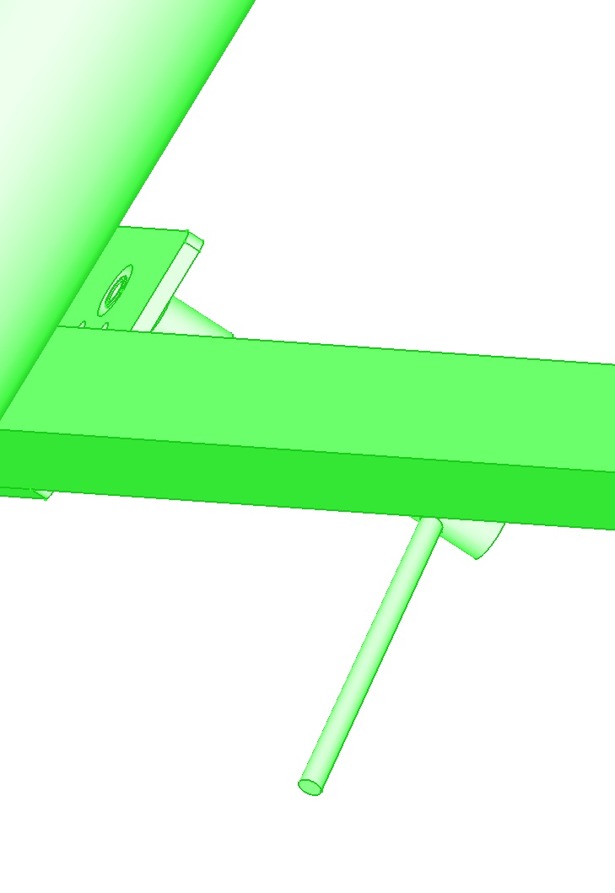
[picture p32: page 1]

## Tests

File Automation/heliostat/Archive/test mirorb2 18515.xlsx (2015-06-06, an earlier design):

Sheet: 180515
nbre pas | PhR G | PhR D | pas max G | pas max D
1380 | 463 | 497 | 1071 | 514
1381 | 463 | 497 | 1071 | 514
1382 | 462 | 497 | 1071 | 514
1383 | 462 | 498 | 1071 | 514
1384 | 462 | 498 | 1071 | 514
1385 | 463 | 498 | 1071 | 514
1386 | 462 | 497 | 1071 | 514
1387 | 460 | 498 | 1071 | 514
1388 | 462 | 498 | 1071 | 514
1389 | 465 | 496 | 1071 | 514
1390 | 462 | 498 | 1071 | 514
1391 | 461 | 498 | 1071 | 514
1392 | 464 | 498 | 1071 | 514
1393 | 462 | 497 | 1071 | 514
1394 | 462 | 498 | 1071 | 514
1395 | 461 | 498 | 1071 | 514
1396 | 465 | 498 | 1071 | 514
1397 | 461 | 497 | 1071 | 514
1398 | 462 | 497 | 1071 | 514
1399 | 463 | 498 | 1071 | 514
1400 | 462 | 498 | 1071 | 514
1401 | 462 | 498 | 1071 | 514
1402 | 462 | 498 | 1071 | 514
1403 | 462 | 498 | 1071 | 514
1404 | 461 | 499 | 1071 | 514
1405 | 462 | 498 | 1071 | 514
1406 | 461 | 496 | 1071 | 514
1407 | 462 | 498 | 1071 | 514
1408 | 462 | 498 | 1071 | 514
1409 | 463 | 498 | 1071 | 514
1410 | 462 | 499 | 1071 | 514
1411 | 462 | 498 | 1071 | 514
1412 | 462 | 498 | 1071 | 514
1413 | 461 | 494 | 1071 | 514
1414 | 461 | 498 | 1071 | 514
1415 | 462 | 498 | 1071 | 514
1416 | 461 | 498 | 1071 | 514
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

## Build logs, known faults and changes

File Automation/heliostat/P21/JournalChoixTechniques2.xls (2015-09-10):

Groupe | Composant | Contrainte | Solution | Avantages | Inconvénients | Bilan | Commentaire
A. Champ de miroirs
1. Structure support
Champ de miroirs | Structure support des miroirs | Orientation | Nord-Sud | Bon suivi du soleil est-ouest | Décalage vers le nord, variable au cours d’une journée et au cours de l’année | Choix principal retenu
Champ de miroirs |  |  | Est-Ouest horizontal | Meilleur suivi du soleil pour des inclinaisons fortes (soleil bas, cas de latitude élevée) | Mauvais suivi des déplacements du soleil d’est en ouest (Décalage de la tache focale vers l’ouest le matin, vers l’est l’après-midi…) | A étudier pour des latitudes élevées….
Champ de miroirs |  |  | Est-ouest incliné | Champ de miroirs orientés de manière optimale vers le soleil | Mauvais suivi des déplacements du soleil d’est en ouest (Décalage de la tache focale vers l’ouest le matin, vers l’est l’après-midi…)
2. Facette miroir
Champ de miroirs | miroirs | matériau | feuille réfléchissante collée | peu cher ? | autre matériau support, rigide et plan, inconvénient de la colle…
 |  |  | tôle alu anodisée | disponibilité, facilité de découpe, réflectivité | flexibilité, nécessité d'un support qui assure la planéité
 |  |  | miroir en verre standard | planéité, bon marché | fragilité, poids
 |  |  | miroir en verre amélioré | planéité, durée de vie, réflectivité | fragilité, poids
Champ de miroirs |  | fixation du miroir au support | pincement aux 4 angles | simple à mettre en œuvre | solidité du maintien
 |  |  | pincement aux 2 extérmités | simple à mettre en œuvre | solidité du maintien
 |  |  | vissage | recyclabilité, durée de vie | déformation locale du miroir
 |  |  | collage | facile à construire ? | recyclage difficile, durée de vie ,
Champ de miroirs |  | largeur | 0.1m | assez fin | trop large pour concentrer sur un tube sans CPC
Champ de miroirs |  | nombre | 20 | concentration intéressante même avec facettes planes… | 20 axes à faire tourner
Champ de miroirs |  | découpe / réalisation | découpe laser | précision | penser à laisser au moins 1 cm de marge autour des pièces à découper (pour positionner dans la machine)
Champ de miroirs | support de la facette miroir | matériau | demi tube de PVC | bon marché, disponible | matériau polluant, manque de rigidité en flexion sur l'axe, précision de la découpe, fixation du miroir et de l'axe
 |  |  | demi rondin de bois | bonne rigidité, facilité de montage | poids, précision de la forme, déformation avec le temps
 |  |  | profilé métallique en V | résistance à la flexion, facilité de recyclage | fixation à penser ?
 |  |  | profilé métallique en U 6cm de large, face plane contre le miroir | recyclage, résistance à la flexion | poids
 |  |  | bambou | écologique, bonne tenue, réplicabilité | maintien de l'horizontalité des facette
Champ de miroirs |  | découpe / réalisation PVC | tubes PVC: couper en deux avec une cale latérale + une marque trait droit sur le tube (en marquant 2 diamètres parallèles : en plaçant le tube horizontal sur une table + cale de 5cm et entaille au cutter au ras de la cale, de part et d'autre. Ficelle tendue entre les deux entailles + marquage à la bombe. Découpe à la scie sauteuse | simple à réaliser, compatible à la scie sauteuse. Pas de problème avec l'évasement (à une extrémité du tube PVC) | précision du coupeur à la scie sauteuse ? | test réalisé avec succès à l'électrolab
 |  |  | Avec scie à ruban. |  |  | à tester
 |  | réalisation (autres matériaux, à détailler)
Champ de miroirs | axe de rotation de la facette | matériau | tige en métal
Champ de miroirs |  | fixation au support de la facette
B. Récepteur
1. Structure support
Récepteur | Structure support du récepteur | Maintenir le récepteur en hauteur | Support en tipi :
Récepteur |  |  | Pied vertical avec haubans | structure plus simple, moins de matériau nécessaire, ajustement de la position précise grâce aux haubans | coulissement de la structure du récepteur plus compliquée à cause des haubans,
Récepteur |  | Garantir l'horizontalité du récepteur dans l'axe latéral et longitudinal | Longueur des pieds arrondis au dessous | évite d'avoir le récepteur trop haut au point plus bas… facilite la réplication des pieds de manière homogène
Récepteur |  | Rigidité dans l'axe
Récepteur |  | Maintenir le récepteur parallèle au champ de miroirs | Guide de positionnement du support du récepteur fixés de part et d'autre du champ de miroirs (pour tipi) | aide au positionnement du récepteur, évite l'écartement des pieds au sol
Récepteur |  |  | rail central (pour pied vertical) | bon positionnement du rail, directement sur le cadre support des miroirs
Récepteur |  | Contrôle du niveau (plan, position) du concentrateur | Pieds réglables à vis aux extrémités du champ de miroir et pour le support du récepteur
Récepteur
Récepteur |  | Suivre le décalage saisonnier/journalier dû à l'inclinaison du soleil vers le sud
2. Cintres
Récepteur | Cintre | Matériau | bois | plus large, plus léger, meilleur isolant thermique | résistance à la chaleur | retenu pour le démonstrateur
 |  |  | métal | plus résistant à la chaleur, plus fin | gros pont thermique
 |  |  | bi-matériau : centre métal et structure bois | résistance à la chaleur, coupe le pont thermique | plus compliqué
Récepteur |  | protection (du rayonnement) | baguettes pour fermer la cavité et protéger l'isolant et les cintres | maintien du miroir au niveau de chaque cintre
 |  |  | papier d'alu | peu cher | peu solide
 |  |  | CPC en une seule pièce, pliée, visée, mise en forme | cavité bien fermée, position du miroir CPC bien ajustée | plus grande pièce à manipuler ? Plus de matière
Récepteur |  | méthode de découpe | CNC | outil plus répandu | moins précis
 |  |  | laser | outil plus précis | moins répandu | retenu à POC21
3. Réflecteur CPC
Récepteur | réflecteur CPC | Matériau | tôle alu anodisée
 |  |  | tôle inox
Récepteur |  | Fixation au centre
Récepteur |  | fixation sur les côtés
 |  | longueur de tronçon | 1m | 2 tronçons seulement | découpeuse laser de 80cm…
 |  |  | 70cm | découpeuse laser utilisable | 3 tronçons
 |  | fixation aux extrêmités des tronçons | recouvrement
 |  |  | sans recouvrement/faible recouvrement | dilatation plus gérable ? | précision de la position des tôles à leur extrémité…
 |  | dilatation thermique longitudinale : Aluminium +1cm/200°C/2m | 3 tronçons de tôle miroir de 70cm, absorbant chacun 3mm, avec fixations sur des trous longitudinaux de 1.5mm minimum : trous de 3mm pour avoir la marge :) | absorbe la dilatation thermique | crée un trou dans la cavité ? |  | http://www.engineeringtoolbox.com/linear-expansion-coefficients-d_95.html
 |  | dilatation thermique latérale : Aluminium +2mm/200°C/40cm | laisser du jeu à froid sur la fixation centrale du réflecteur ? |  |  |  | http://www.engineeringtoolbox.com/linear-expansion-coefficients-d_95.html
Récepteur | isolant | matériau, épaisseur | laine de roche | bon marché, matériau répandu et efficace | fibres cancérigènes
 |  |  | nouvelle laine de roche aspect cotonneux | pas de fibres cancérigène
 |  |  | coton recyclé + tissu "jean" en protection | matériau organique | tenue en température
 |  |  | laine de mouton | matériau organique | disponibilité
Récepteur |  | protection (du rayonnement) | papier d'aluminium | peu cher | fragile
Récepteur | capot supérieur | matériau | tôle flexible, suivant l'arrondi | une seule pièce, bonne protection des intempéries, facilité de pose
 |  |  | tôle (épaisseur ?) pliée
 |  | fixation sur les côtés | fixation à l'extérieur des L support
 | fermeture aux extrémités | jonction avec le capot | à penser…
 |  | passage de la poutre carrée | à penser…
 |  | passage du tube | à penser…
 |  | jonction avec la vitre ? | à penser…
Récepteur | vitre | matériau, épaisseur
Récepteur |  | fixation
 |  | longueur de tronçon | 1m
 |  | jonction des tronçons | ouverte
 |  |  | joint ? Quel matériau ?
 |  | dilatation du verre : +1mm/200°C/1m |  |  |  |  | http://www.engineeringtoolbox.com/linear-expansion-coefficients-d_95.html
4. Tube absorbeur / chaudière
Récepteur | Tube absorbeur | matériau | acier
 |  |  | inox | applications alimentaires directes | coût, savoir-faire pour le circuit hydraulique…
 |  | dilatation longitudinale : +0.5cm/200°C/2m pour l'acier |  |  |  |  | http://www.engineeringtoolbox.com/linear-expansion-coefficients-d_95.html
5. Montage
Récepteur | récepteur | assemblage | ?
C. Système de suivi
1. Moteurs
Champ de miroirs | moteur | fixation à l'axe de la facette
Champ de miroirs |  | fixation au support du champ de miroirs
Suivi des miroirs | Moteurs | nombre | 20 | plus flexible pour tester différentes configurations : variation de la hauteur du récepteur, position latérale du récepteur… | 20 moteurs à acheter, à piloter, à alimenter
Suivi des miroirs |  |  | 1 | plus économique, plus low-tech ? | transmission mécanique nécessaire, précision associée
Suivi des miroirs |  | type | pas à pas | précision de pilotage (même à une fraction de pas…) | consommation électrique en permanence…
Suivi des miroirs |  |  | DC | plus répandu | précision ?
Suivi des miroirs |  | puissance | à calculer / tester ?
2. Capteurs optiques
Suivi des miroirs | Capteurs optiques | contrôle position moteur | interrupteur activé à une certaine position du moteur (bosse sur une pièce ronde…) | low-tech? | précision, une seule position détectable
 |  |  | potentiomètre | plus simple, donne l'info de position pour tout angle du moteur | ?
Suivi des miroirs |  | contrôle direction rayon réfléchi | photo-résistance |  |  | tester au début
 |  |  | photo-diode |  |  | retenu pour la suite
3. Circuit de contrôle-commande
Suivi des miroirs | Controleur-commande | arduino |  | open source
4. Code logiciel
Suivi des miroirs | Software
D. Exemple d’usage
1. Hammam
a) Circuit hydraulique
Circuit hydraulique | tuyauterie | circuit
Circuit hydraulique |  | longueurs, diamètres
Circuit hydraulique | échangeur | dimensions, capacité
b) Structure
Usage | hammam | construction
Usage |  | isolation
2. Cuiseur
a) Circuit hydraulique
Circuit hydraulique | tuyauterie | circuit
Circuit hydraulique |  | longueurs, diamètres
Circuit hydraulique | échangeur | dimensions, capacité
b) Structure
Usage | plaque de cuisson | échangeur
Usage |  | isolation
Usage | cocotte minute double paroi | échangeur
Usage |  | isolation
Usage | bouilloire | échangeur
Usage |  | isolation
Usage | stérilisateur de bocaux… | isolation
Usage
Journal des choix techniques (et esthétiques ?), avec justification des choix, ressources…
Sous forme de tableau : réorganiser le tableau pour faire apparaître la structure du rapport, lier les parties conception/réalisation

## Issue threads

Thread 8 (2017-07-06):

Interesting proposal to create a Solar Workbench in FreeCAD

luzpaz, 2017-07-06:
https://forum.freecadweb.org/viewtopic.php?f=8&t=22943&p=181357

luzpaz, 2020-03-10:
Any progress on this ?

Cywil23, 2020-03-10:
Progress about our solarconcentrator? (No, our group is in stand by since a while)
Or about the project in the link you sent? (No idea)

luzpaz, 2020-03-10:
about the former. sorry to hear.

Cywil23, 2020-03-10:
Sorry, I forgot that the 3D model on this repository is not the last one.

Our last documentation :
https://www.instructables.com/id/Solar-OSE-Solar-concentrator-for-steam-generation/

But no ressources now to develop the good dimensions prototype

luzpaz, 2020-03-11:
Thanks for the heads up. Don't be a stranger on the FreeCAD forum. There are others there that are interested in this sort of thing so...

Cywil23, 2020-03-11:
Thanks for this advice, but we abandoned freecad for the development of our project, because at the time (2015), the macro that replaced the assembly module was really not powerful enough to allow us to make our 3D model.
I don't know the step of the development of this module now...

luzpaz, 2020-03-11:
There are several options now for assembly. * *
* Assembly2+
* Assembly3
* Assembly4

Cywil23, 2020-03-11:
Nice, thanks. I will take a look (when I'll come back on total open source hardware project...)

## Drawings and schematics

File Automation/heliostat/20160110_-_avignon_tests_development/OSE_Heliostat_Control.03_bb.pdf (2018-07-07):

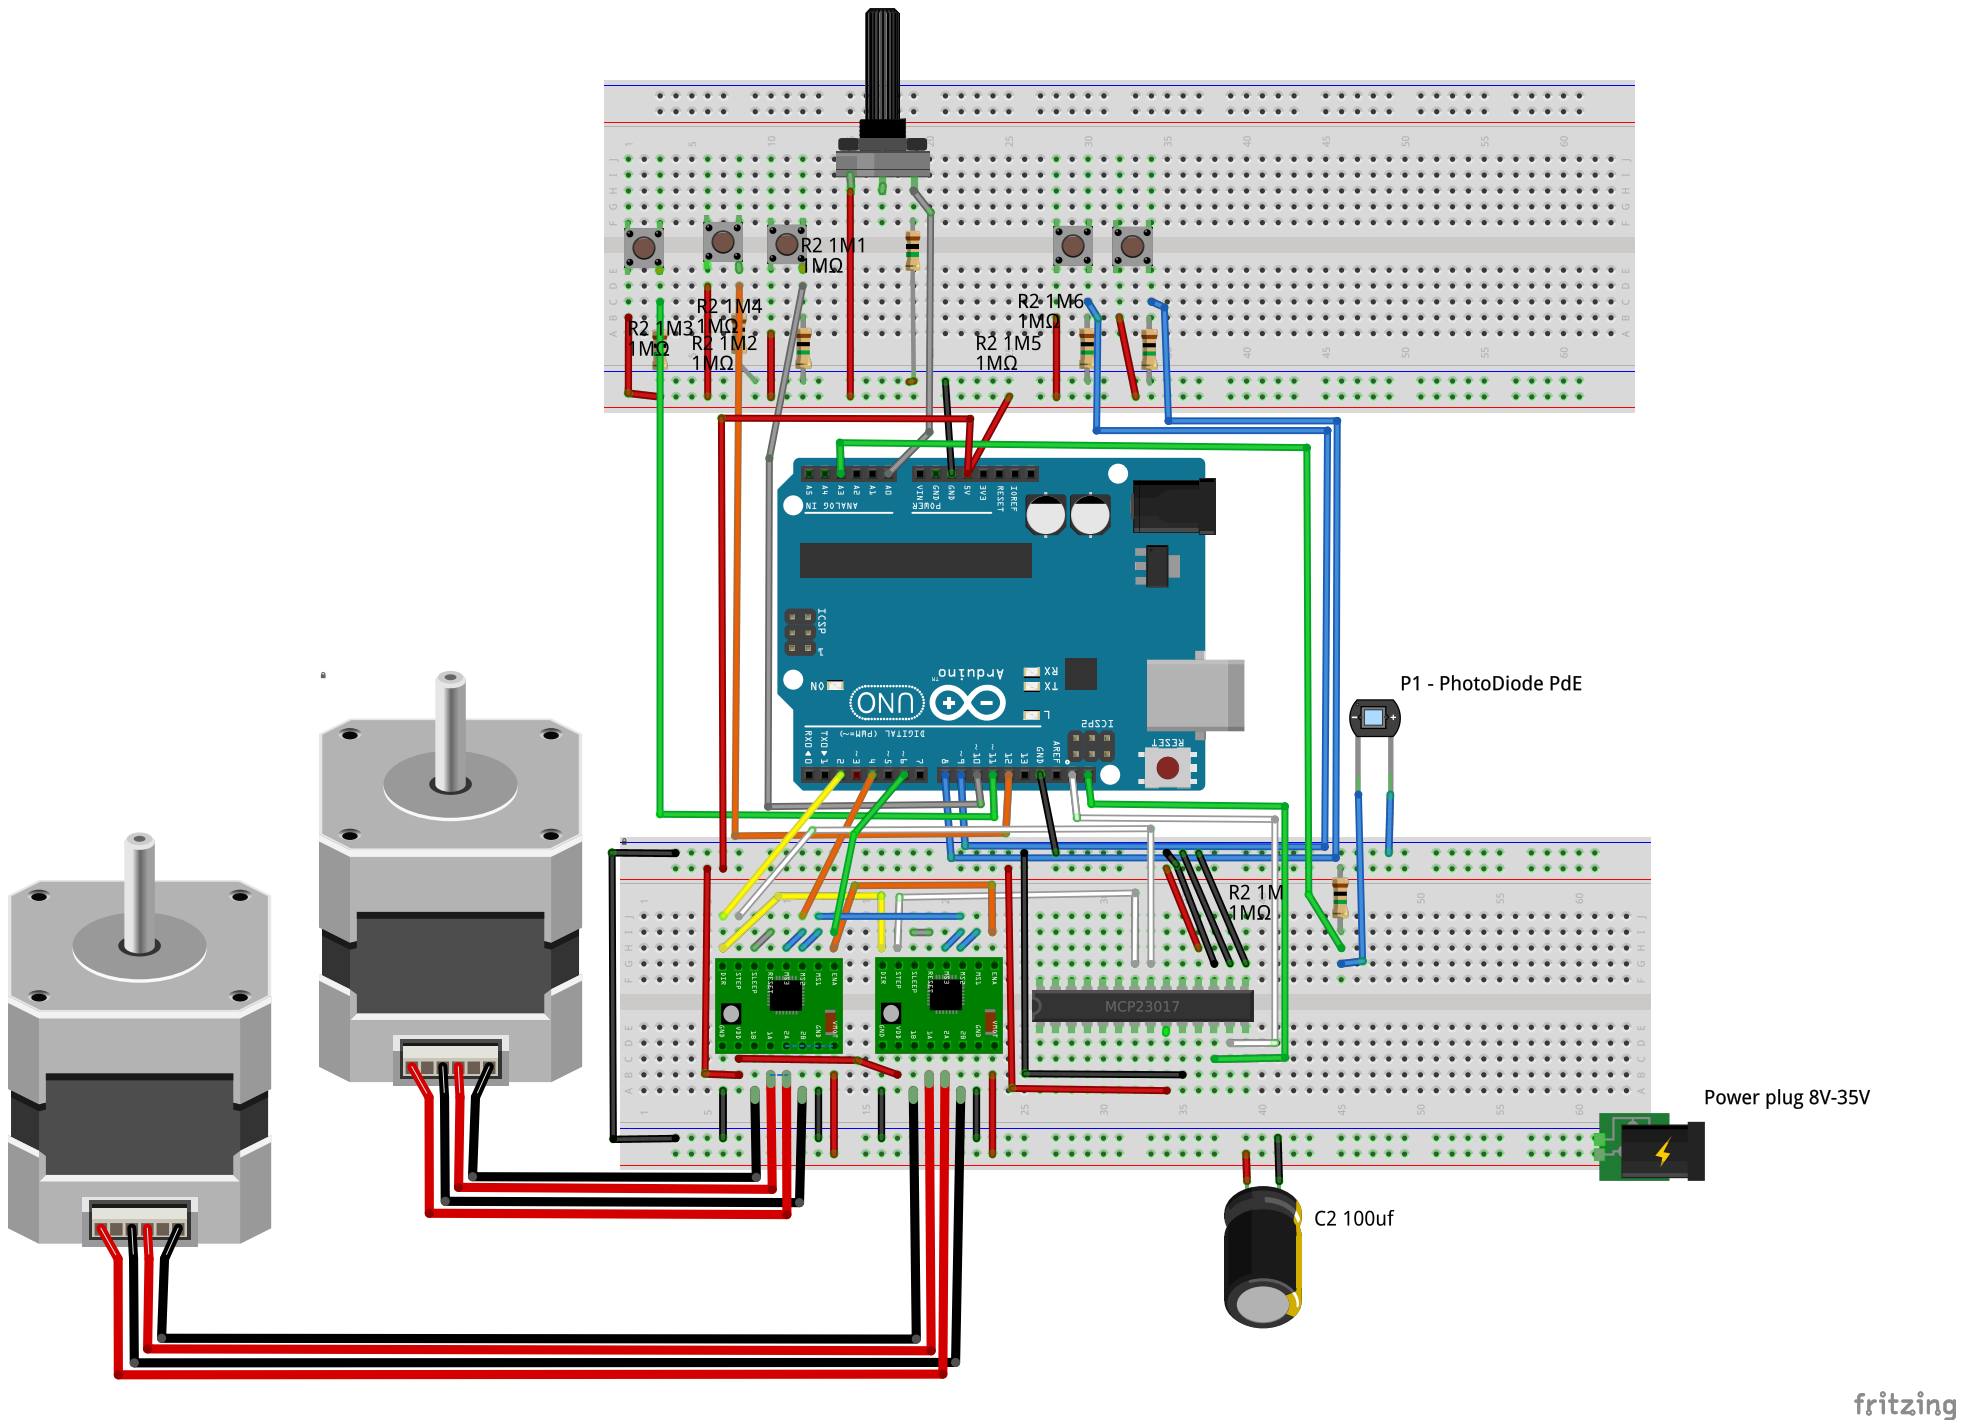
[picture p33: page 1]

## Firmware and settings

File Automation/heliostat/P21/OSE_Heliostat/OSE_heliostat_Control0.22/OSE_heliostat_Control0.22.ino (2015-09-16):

#include <Wire.h> // to control the MCP23017 to control the step on all motors

//**************************************************************
//  Open Souce Écologie - Solar Heliostat controller
//  Name: SeguiLSol25
//  Authors: Andrea Sannuto @ndrsan, Jean Walter , Remi @Remi_R, Cherif 
//  Website: www.osefrance.fr  @OSE_Fr
//  Rev 001 
//  Date 08 April 2015
// features, micro step to follow the sun or heliostat with 1 axis only, as fast as it can to be the most precise.  
// this software is released under the GPL V.3 
// for more recents update, check out the git page: https://github.com/osefrance/SolarConcentrator
// http://bit.ly/1JnwSGd
//**************************************************************


// 5 main functions (to translate in class)
// function 0 = Awake
// function 1 = Find Midpoint / calibration : it must correct the steps based on the speed the sun is moving.
// function 2 = Offset mirror x to keep the photodiode always slightly under the threshold(or a special threshold) in order to drive all motors to the central position of the 
// function 3 = Heliostat / Follow the sun, thanks to the offset mirrors and the interrupts of the photoresistors positioned on the edge of the absorber
// function 4 = sleep. go in position to sleep and sleep.

// Status / Change log:
// Function 1 Calibration implementation without time check.  
// Function 3 working based on the feedback from the PdE. moves all mirrors at once when PdE reaches the threshold. slightly modified need to be retested.


// Stepper driver Pin configuration  - set up based on Pololu A4988 driver although also DRV8825 will be integrated in this design.

const int mirrorsQ = 2 ; // how many mirrors should be controlled. if through the MCP23017 they should be connected incrementally starting from port A0 of MCP23017
int mirrorsQbin = 1; // mirrorsQconversion to consecutive bits rappresenting each single motors
// int stepPin[] = {3, 5, 7}; // used only if STEP is directly connected to the arduino. not used in case of going through the i/o extender MDCP 32017.  high and low cycle makes 1 step of the stepper . minimum 1 uSec per state - "A low-to-high transition on the STEP input sequences the translator and advances the motor one increment. "

int mirrorSel = 1; // index for the mirror selector when using the MCP23017 it will be set to 255 to step on all motors at the same time (set to 0 if used as index for stepPin[] matrix, set to 1 if used as pointer for the MCP23017 port extender

const int dirPin = 2;  // This determines the direction of rotation of the motor. Changes to this input do not take effect until the next STEP rising edge.
const int enablePin = 6; // This input turns on or off all of the FET outputs. When set to a logic high, the outputs are disabled. When set to a logic low, the internal control enables the outputs as required. The translator inputs STEP, DIR, and MSx, as well as the internal sequencing logic, all remain active, independent of ENABLE input state.
const int microStepPin = 4; // This input turns on or off all of the FET outputs. When set to a logic high, the outputs are disabled. When set to a logic low, the internal control enables the outputs as required. The translator inputs STEP, DIR, and MSx, as well as the internal sequencing logic, all remain active, independent of ENABLE input state.



const int endStopPin[] = {8} ; // the pin of connection of the endstop. should use a i/o port extender as input in stead of the direct Arduino ports.

// pin settings
int pushWButPin = 12; // push button to move motors manually to West of 1 (micro)step
int pushEButPin = 11; // push button to move motors manually to Est of 1 (micro)step
int pushCalibrateButPin = 10; // push button to start the calibration sequence. temporarily activated manually for development purpose... *** to integrate in circuit ***

int potPin = A0; // potentiometer to set the movement speed of the motor - temporary setting

// Joystick control
int jButPin = 13;
// int jPotxPin = A3;
// int jPotyPin = A1;

// DEBUG MODE 1 on, 0 off. check serial for output of the variables value.
 int debugmode = 0;
// int debugmode = 1;


// Variables
const int dirEst = 1; // Change this to correct toward east direction movement of the motors. 
const int dirWest = 0; // Change this to correct toward est direction movement of the motors.  
// int dir ; // set the direction --- removed if using dirEst / dirWest
int spd ; // set the speed - the higher the slower

// initialize the matrix of position based on time ****
int stepsEl[mirrorsQ] ; // initialize the stepsEl variable
int stepsEh[mirrorsQ] ;  // initialize the stepsEh variable
int timeEl[mirrorsQ] ; // initialize the timeEl variable
int timeEh[mirrorsQ] ; // initialize the timeEh variable
int rayWidth[mirrorsQ] ;  // initialize the raywidth variable

// photosensor related variables

const int pdPin[]= {A3} ; // matrix of the photodiodes. - say A3 for the east photodiode (PdE in the schematics) and Ax for the western one (PdW). PdE is the driving photodiode triggering the motors to step when PdE gets in the sun blade reflection. PdW should be mostly used for calibration only but testing if it can be removed.
const float pdThreshold = 3 ; // threshold at which the sun hits the photodiode, used for calibration and for heliostat function

void setup() {

/*
setup of motor's pins connected on the arduino - commented out when using the MCP23017
for (int a=0; a<mirrorsQ; a++){
  pinMode(stepPin[a], OUTPUT);
}
*/

pinMode(dirPin, OUTPUT);
pinMode(enablePin, OUTPUT);
pinMode(microStepPin, OUTPUT);
pinMode(pushWButPin, INPUT);
pinMode(pushEButPin, INPUT);
pinMode(pushCalibrateButPin, INPUT);


// MCP23017 setup

 Wire.begin(); // wake up I2C bus

// set I/O pins to outputs

 Wire.beginTransmission(0x20);
 Wire.write(0x00); // IODIRA register
 Wire.write(0x00); // set all of port A to outputs
 Wire.endTransmission();
 Wire.beginTransmission(0x20);
 Wire.write(0x01); // IODIRB register
 Wire.write(0x00); // set all of port B to outputs
 Wire.endTransmission();

 if (debugmode == 1) { Serial.begin (9600); }
 
 for (int a=1; a<= mirrorsQ; a++) { // converts the decimal quantity to binary for later comparison when switching from one motor to the next
   mirrorsQbin= mirrorsQbin * 2;
   }
}

void loop() {
   // put your main code here, to run repeatedly:
   digitalWrite(enablePin,LOW ); // set to low to keep the stepper motors engaged in the position. it consumes power but essential in direct drive with environmental perturbances (wind) 
   digitalWrite(microStepPin, HIGH); // microstepping enabled (based on hardware configuration HHH = 1/16th)
   // digitalWrite(microStepPin, LOW); // microstepping disabled
  
   // int jButRead = digitalRead(jButPin);
  
  if (digitalRead(jButPin) == HIGH )   { 
      selectMirror(); 
      }
  
  if (digitalRead(pushWButPin) == HIGH ) {
      turn(dirWest,mirrorSel);//moves the mirror(s) toward West
      return ;
      }

  if (digitalRead(pushEButPin) == HIGH ) {
      turn(dirEst, mirrorSel);//moves the mirror(s) toward East
      return ;
      }  
  
  if (digitalRead(pushCalibrateButPin) == HIGH ) {
      calibrate(); // launches the calibration function 
      offsetPosition (); // set the mirror x to the offset position in order to highlight the photodiode 
      return ;
      } 
  
  
  heliostat(); // keeps the photodiode always under the threshold and moves all mirrors when the reading is higher than the threshold


}

void turn (int dirT, int spin){
    digitalWrite(enablePin, LOW);
    digitalWrite(dirPin, dirT);

  spd = map(analogRead (potPin), 1023, 780, 1,3000);
/*  digitalWrite(stepPin[spin], HIGH);
  delayMicroseconds(spd);
  digitalWrite(stepPin[spin], LOW);
  delayMicroseconds(spd);
*/

   // turn A Ports ON based on mirrorSel (Make 1 step)
if (debugmode == 1) {   Serial.println (spin); }
  Wire.beginTransmission(0x20);
       Wire.write(0x12); // GPIOA
       Wire.write(spin); // port A
  Wire.endTransmission();
     // B Ports
  /*   Wire.beginTransmission(0x20);
       Wire.write(0x13); // GPIOB
       Wire.write(a); // port B
     Wire.endTransmission();
  */
  delayMicroseconds(spd); // Delay will be removed with a state-machine variable ****

  // turn OFF A Ports
 
  Wire.beginTransmission(0x20);
       Wire.write(0x12); // GPIOA
       Wire.write(0x00); // port A
  Wire.endTransmission();
     // turn off B Ports
 /*    Wire.beginTransmission(0x20);
       Wire.write(0x13); // GPIOB
       Wire.write(0x00); // port B
     Wire.endTransmission();
  */
 
delayMicroseconds(spd); // Delay will be removed with a state-machine variable ****

if (debugmode == 1) {   Serial.print ("mirrorSel ; mirrorsQbin");  Serial.print (mirrorSel); Serial.print (" ; "); Serial.println (mirrorsQbin); }

}

void selectMirror() {
      mirrorSel = mirrorSel *2;
      if (mirrorSel > mirrorsQbin) { mirrorSel = 1;}
      while (digitalRead(jButPin) == HIGH )   {}
    }

float readPd (int photoDiodedPin) // read the photo diode 
{
int pdRead = analogRead( photoDiodedPin);
float pdVolt = pdRead / 1024.0 * 5.0;  // can be avoided to have a float variable as the pdread can be used directly and threshold can be set with a  value between 1 and 1024. ****
if (debugmode == 1)
  {
  Serial.begin (9600);
  Serial.print("inside readPD sub-Function : pdVolt ; pdRead = ");
  Serial.print(pdVolt);
  Serial.print(" ; ");
  Serial.print(pdRead);
  Serial.println();
  }
 
return pdVolt;
}

void heliostat(){ // keeps the reflected image of the sun of all mirrors centered to the receptor, by keeping the photodiode signal under the threshold

  if (debugmode == 1) {   Serial.print ("inside the heliostat function");  }
  
  //  following part is duplicated in findERW() just mirrorSel should be 255 to move all mirrors in stead of anything else. Heliostat() function can be simplified to call a modified version of findERW ****
  
  float pdreading = readPd (pdPin[0]);
  while(pdreading < pdThreshold)  {
      turn(dirEst, 255);//moves all mirrors
      pdreading = readPd (pdPin[0]);
      }  
}  

void calibrate(){ // performs the calibration sequence and memorize the matrix of values = Find0, FindEl event, FindEh event, perform the correction check,
  find0(); // Find the 0 position of each mirrors
  findERW(); // find the ray width on the eastern sensor per each motor
  //  findCorrection ();   // find the correction factor in term of steps per minute that should be applied to the mid position of each blade 
  //  midPosition (); // set all motors to the mid position 
 
} 

void find0(){ // find the 0 position for all mirrors
  mirrorSel = 1;
  for (int i = 0; i < mirrorsQ; i++) { //   sets all mirrors to 0 position
    while (endStopPin == LOW) { 
         turn(dirWest, mirrorSel);//moves the mirror(s)
    }
    selectMirror();
  }
}


void findERW(){ // find the ray width on the eastern sensor AKA:
// it creates the matrix informations with: 
// a- the number of steps (steps-el[n]) and the time (time-el[n]) when the eastern photodiode was hit by the reflected sun ray (voltage pdreading  lower than threshold)
// b- the number of steps (steps-eh[n]) and the time (time-eh[n]) when the eastern photodiode was left by the reflected sun ray (voltage pdreading higher than threshold)
// c- it defines the difference of steps that defines the ray-width at a given time for the selected mirror : rayWidth[n] = steps-eh[n]- steps-el[n]

// this function is almost duplicate with the find0() function, only direction and trigger changes. also to find El and Eh events is about the same code. can be further simplified. ****
  
  mirrorSel = 1;  // all the rest is executed starting from the first mirror. it can be improved to let select the mirror[x] inside the parent function and loop it in there. ****
  for (int i = 0; i < mirrorsQ; i++) { //   loops to work on all mirrors one after the other
 
     float pdreading = readPd (pdPin[0]); // updates the pdreading before entering the loop. I could readPd(pdPin[0]) inside the while condition and remove 2 lines of code (? to test) ****
     while(pdreading < pdThreshold)  {
      turn(dirEst, mirrorSel);//moves the mirrors one by one
      stepsEl[i]++; // increase the steps counter of 1 while in the loop.
      pdreading = readPd (pdPin[0]); // updates the pdreading at the end of the loop
      }
      // timeEl[i] = currentTime();  **** develop the function current time based on the clock DS1302 (yet to integrate)
      stepsEh[i] = stepsEl[i]; // increase the steps counter of 1 while in the loop.
      while(pdreading > pdThreshold)  {
      turn(dirEst, mirrorSel);//moves the mirrors one by one
      stepsEh[i]++ ;// increase the steps counter of 1 while in the loop.
      pdreading = readPd (pdPin[0]); // updates the pdreading at the end of the loop
      }
      // timeEh[i] = currentTime();  **** develop the function current time based on the clock DS1302 (yet to integrate)
   rayWidth[i] = steps-eh[i]- steps-el[i];
   selectMirror(); // select the next mirror
   if (mirrorSel == 1) { return;}
  }
}


/*
Board	I2C / TWI pins
Uno, Ethernet	A4 (SDA), A5 (SCL)
Mega2560	20 (SDA), 21 (SCL)
Leonardo	2 (SDA), 3 (SCL)
Due	20 (SDA), 21 (SCL), SDA1, SCL1

MCP23017 I2C chip
SCL = 12
SDA = 13

// pins 15~17 to GND, I2C bus address is 0x20
*/

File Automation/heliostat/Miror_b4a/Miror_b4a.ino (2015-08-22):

 
  //STEPPER
  int stepPin[] = {31, 37, 43}; // pin 31 motor 0; 33 motor 1; 35 motor 2 (yellow wires)
  int dirPin[] = {33, 39, 45}; // pin 33 motor 0; 33 motor 1; 35 motor 2 (white wires)
  int enablePin[] = {35, 41, 47}; //pin 35 motor 0; 33 motor 1; 35 motor 2 (green wire)
  int stepping; // Pin value for loops (yellow wires)
  int sensrot; // Pin value for loops (white wires)
  int enabling; //Pin value for loops (green wire)
  int M;//motor number 0 to 2, 1 center

  //int a0;// steps totolizer motor 1
  //int a1;// steps totolizer motor 2
  //int a2;// steps totolizer motor 3
  
  //int stepscount; //number of steps totaliser, will be set to 0 during miror zeroing - Cma also zeroed then
  int aLmax;//value of a at reading of the peak brithness of the left photoresistance within loops
  int aRmax;//value of a at reading of the peak brithness of the left photoresistancewithin loops
  //int a0Lmax;//value of a at reading of the peak brithness of the left photoresistance
  //int a0Rmax;//value of a at reading of the peak brithness of the left photoresistance
  //int a1Lmax;//value of a at reading of the peak brithness of the left photoresistance
 // int a1Rmax;//value of a at reading of the peak brithness of the left photoresistance
 // int a2Lmax;//value of a at reading of the peak brithness of the left photoresistance
 // int a2Rmax;//value of a at reading of the peak brithness of the left photoresistance

  int a;//steps within loop
  int x;//all purpose varaible; delta reading between peak photoresistance and current reading
  int y;// all purpose variable
  int z;// all purpose variable
  int stepscount;//variable for calculations within loops
  
   // OPTIC SENSORS: PHOTORESISTANCES, THERMISTANCES ET  PHOTOVOLTAIC CELL
  int PhL = A0; // left photoresistance RED wire
  int PhR = A1;// right photoresistance MARON wire
  int PhLA;//lecture analogique A0 horizontale gauche
  int PhRA;//lecture analogique A1 horizontale droite
  int peaks; // number of steps indicating  both peaks have been passed
  int peakL;//number of steps corresponding to peak of left photoresistance
  int peakR;//number of steps corresponding to peak of right photoresistance
  int DeltaPhL;// photoresistance reading - maximum value of past readings
  int DeltaPhR;// photoresistance reading - maximum value of past readings
  int Insol;//indicator of insolation: average reading of two photoresistances
  int PhLmax;//lecture la valeur maximale en PWM de la photoresistance gauche
  int PhRmax;//lecture actuelle de la valeur en PWM de la photoresistance droite
  int ThL = A4;//left thermistance, WHITE wire
  int ThR = A5;// right thermoresistance, PURPLE wire
  int ThLA;//analog reading of left thermistance
  int ThRA;// analog reading of right resistance
  int LedYL = A14; //Left yellow LED (green wire)
  int LedYR = A15;// Right yellow LED (blue wire)
  int LedYLA; //Analog reading of left yellow LED
  int LedYRA; //Analog reading of right yellow LED

  
    //PUSH PIN TO INITIATE A MIROR SEARCH FOR THE CENTRAL RECEPTOR  
  int pushbut = 22;// push button to start serach
  int pushbutstate;// push button state reading:
  int FDCM[] = {24, 26, 28}; // pin 24 fin de course 0 (blue); 26 Fin de course 1(center, white); 28 motor 2 (green)

  
  void setup() {
    Serial.begin(9600);
    pinMode(pushbut, INPUT);
    pinMode(dirPin[2],OUTPUT);
    pinMode(stepPin[2],OUTPUT);
    pinMode(enablePin[2], OUTPUT);
    digitalWrite(enablePin[2],LOW); // Set Enable low
    pinMode(dirPin[1],OUTPUT);
    pinMode(stepPin[1],OUTPUT);
    pinMode(enablePin[1], OUTPUT);
    digitalWrite(enablePin[1],LOW); // Set Enable low
    pinMode(dirPin[0],OUTPUT);
    pinMode(stepPin[0],OUTPUT);
    pinMode(enablePin[0], OUTPUT);
    digitalWrite(enablePin[0],LOW); // Set Enable low
    }
  
  void loop() {// MOTOR 1 ONLY (CENTRAL MIROR)
   peakL = 0;  //reset left peak indicator
   peakR = 0;  //reset right peak indicator
   peaks = 0;  //reset peak indicator
   PhLmax = 0;  //reset left Photoresistance max value 
   PhRmax = 0;  //reset right Photoresistance max value
  pushbutstate = digitalRead(pushbut);  // readi if the push button to start a centering procedure is ON
  if (pushbutstate == HIGH ) {
    M = 1;
    sensrot = dirPin[M];
    stepping = stepPin[M];
    while (FDCM[M] == LOW){//  ZEROING MIROR-MOTOR 1
      digitalWrite(sensrot,HIGH); // gives direction
      turn();//miror moves until position switch faces ground
    }
    a = 0;//ste motor positions in steps set to zero
    search();   //a module that search for the two peaks
   }  // the two peaks ahve been identified, we now move the miror back the the centrola point between the peaks 
   
   //PROGRAM STARTS HERE IF PUSH BUTTON IS OFF
   ThLA = analogRead(ThL);//left thermistance reading
   ThRA = analogRead(ThR);// right thermistance reading
   z= ThLA-ThRA;
   y = abs(z);
   y = y - 15;//correction for differential between thermistance (no sun)
  Serial.print("therm gauche");
  Serial.print(",");
  Serial.print(ThLA);
  Serial.print(",");
  Serial.print("therm droite");
  Serial.print(",");
  Serial.print(ThRA);
  Serial.print(",");
  Serial.print(" Delta therm");
  Serial.print(",");
  Serial.print(z);
  Serial.print(", ");
  Serial.print("PhR G");
  Serial.print(",");
  Serial.print(PhLA);
  Serial.print(",");
  Serial.print("PhR D");
  Serial.print(",");
  Serial.print(PhRA);
  Serial.print(","); 
  Serial.print("insolation");
  Serial.print(",");
  Serial.print(Insol);
  Serial.println(",");     
   if(y > 30){//activate motor if differatial temperature between therm exceeds 30 ua
     if(z < 0){//checks for which direction the motor should be set
       digitalWrite(sensrot,HIGH); // change direction
         for(x=0; x<33;x++){
           turn();
           a = a +1;
         }
         Serial.print("step");
         Serial.print(",");
         Serial.print("1");
         Serial.print(",");
        }
      else{
         digitalWrite(sensrot,LOW); // change direction
         for(x=0; x<34;x++){
           turn();
           a = a - 1;
         }
         Serial.print("step");
         Serial.print(",");
         Serial.print("-1");
         Serial.print(",");
         }
       }
       else{
          Serial.print("step");
         Serial.print(",");
         Serial.print("0");
         Serial.print(",");
         }
   }
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

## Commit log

2015-02-09 first draft by Guillaume
    [06_ligne de miroirs.stl, 07_support miroirs.stl, 08_collecteur.stl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]
2015-04-11 first heliostat program for the solar concentrator. it features a simple microstepping of 1/16th of 200 full steps stepper motor and makes a microstep every 54seconds or so.
    will need to add:
    release 1:
    - reset to 0 position using an optical sensor
    - first setup on the morning (need rtc implementation) using 2 light sensors on the absorber edges
    - last setup on the evening in order to understand the error and use the new delay time for the day after.
    release 2:
    - multiple mirrors using an IC (need wire implementation)
    release 3:
    - safety shut off of the mirrors
    - statistical information
    ...
    [SeguiLSol25.ino]
2015-04-11 added comments.
    it features a simple microstepping of 1/16th of 200 full steps stepper motor and makes a microstep every 54seconds or so.
    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
    [SeguiLSol25.ino]
2015-04-11 Adding the first schematic for the seguilsol25 scatch.
    this features a simple microstepping functioning.
    [SeguiLSol.fzz]
2015-04-11 added fritzing picture of the schematic
2015-04-18 moved the tube toward the center in order to get the reflected light. need to test if moving the source will keep the sun against the tube, else need to move the tube again.
    to move the tube: Tseparator kit, translation, set to 0 0.02 0 (X Y Z)
2015-04-23 added L1 and L2 to circuit (photoresistor to allow to find the center of the absorber), minor changes to the code.
    [SeguiLSol.fzz]
2015-05-09 adding jean modif
    added new scatch developed by Jean and fritzing schematic for UNO
    including photo resistors
2015-05-14 adding latest 3d design on Freecad, designed by Cywil, redesing freecad by AlainT
    [ASM CS.FCStd, Accouplement.FCStd, Coussinet lub.FCStd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]
2015-05-27 programmes matlab
    calcul de la position du soleil
2015-05-30 Maquette 3D Inventor
    Ajout de la maquette numérique 3D sous Inventor
    [Accouplement.ipt, Assemblage absorbeur E-O.0010.iam, Assemblage absorbeur E-O.iam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]
2015-05-30 premier test de push
2015-05-30 ceci est le teste de cherif
    ceci est le teste de cherif
2015-05-30 Ajout datasheet
    Ajout de la datasheet du composant d'horloge
2015-05-30 alain modif
    modif de alain
2015-06-01 library of clock
    Bibliothèque arduino de l'horloge DS1 302
2015-06-06 created folder Automation that includes all general electronic documents and all programs and electronic specific to each function
    Please enter the commit message for your changes. Lines starting
    [SeguiLSol.fzz]
2015-06-06 Excel file showing recording of photoresistance response while rotating the mirors; method to identify two peaks corresponding to the two photoresistances Frtizing with switch to change from full ste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
    [SeguiLSol 2.fzz, test mirorb2 18515.xlsx]
2015-06-06 issues with microstep function or peak left as it founds after 1 cycle of full step as if it had a peakL, indipendently by the mirror position.
    [Miror_b3.1.ino, Miror_b3.ino]
2015-06-07 solved issue that was setting microTrig to 1 after first cycle,
    [Miror_b3.1.ino]
2015-06-11 Maquette numérique Concentrateur Solaire FreeCAD
    [Accouplement.FCStd, Axe_D4.FCStd, Axe_D8.FCStd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]
2015-06-13 modification pour éviter confusions entre a totaliseur de pas et microsteps pour itération module de calcul pour suivre l'horloge
2015-06-20 OledHorloge
    Mise en oeuvre de l'affichage de l'heure sur afficheur Oled
2015-06-21 fichier manquant
    prog matlab passe de l'heure légale décimale à l'heure solaire
2015-06-27 calculs sur le CS
    dans ce dossier programmes pour calculer le CPC, et les angles et
    paramètres géométriques du miroir de Fresnel
2015-07-17 Sketch et branchements pour Mega, 3 moteurs et capteurs optiques (photorsistances, LED, Thermistances et cell photovoltaique)
    [SeguiLSol 3.fzz]
2015-08-14 Petit sketch destiné à enregistrer la réponse des différents capteurs lors de la rotation d'un miroir 2 photorésistances, deux LEDs, deux thermistances et une cellule photovoltaique
2015-08-14 Sketch centrage optique de 4 miroirs
2015-08-22 added graphic of the automation main devices, reorganized variables
    [SeguiLSol 2.fzz, SeguiLSol.fzz, test mirorb2 18515.xlsx]
2015-08-22 reorganized the files and added the sensor and motor layout
    [SeguiLSol 2.fzz, SeguiLSol 3.fzz, SeguiLSol.fzz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]
2015-09-10 most recent program under test is "OSE_heliostat0.21" together with the fritzing circuit. added also the program logic and the open source manual developped so far by the team (Thanks to Francois)
    [JournalChoixTechniques2.xls, OSE_Heliostat_Control.021.fzz, StepperPowerTriacCircuit.fzz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]
2015-09-12 heliostat control 0.22 contains the initial features of the calibration function. check the logic layout for further information together with the electronic layout done in fritzing.
    [OSE_Heliostat_Control.022.fzz]
2015-09-16 new version of 0.22 integrating the intial parts of the calibration function, still untested and not completed. new version of 0.21b to be applied on the relative electronics. based on this program a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
    [OSE_Heliostat_Control.021b.fzz, OSE_Heliostat_Control.022.fzz]
2015-09-25 added control and tested up to 14 motors, need to test the sequencial switching of the motors from port a and port b and from first IO extender to second
2016-01-10 new version of ose heliostat control 0.3 ready for physical testing. integrated - functions to follow the sun with photodiode. - photodiode threshold controlled by potentiometer. - software ready for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
2016-01-12 enable the stepper motors (hold torque) with the push button connected on pin 9 follow the hold variables and function. Also updated the fritzing layout to match the buttons layout.
    [OSE_Heliostat_Control.03.fzz]
2018-07-07 added pdf for circuit sample with 2 motors. final circuit has 20 motors
